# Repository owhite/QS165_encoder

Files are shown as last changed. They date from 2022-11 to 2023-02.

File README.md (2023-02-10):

# QS165 motor magentic encoder with hall output

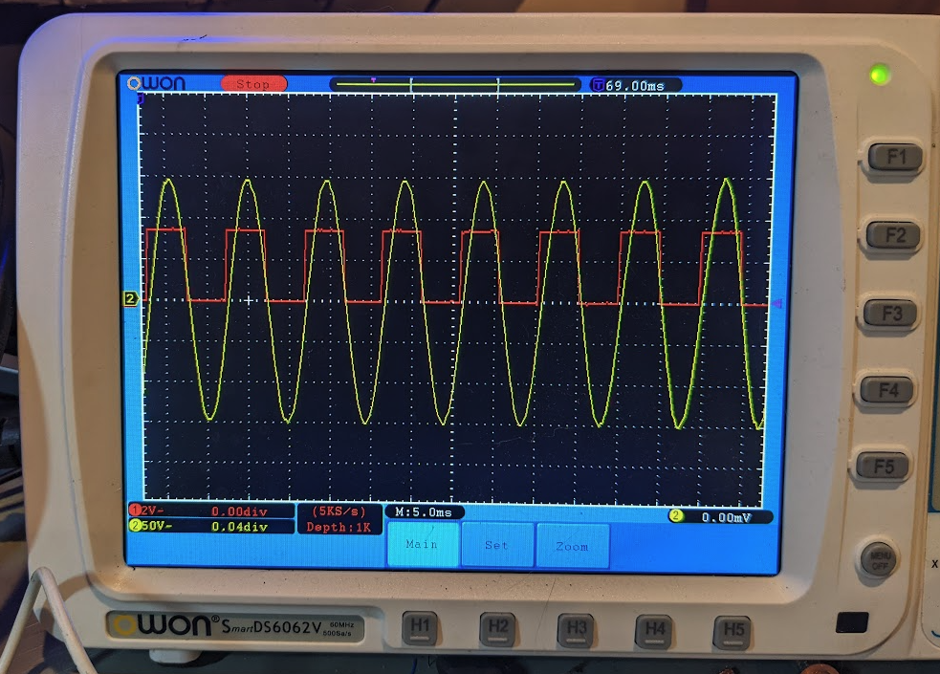
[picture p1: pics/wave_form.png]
phase plus encorder out

One scope probe (red) connected to "W" output of board, and another probe (yellow) is tied to the phase output of the QS165. The QS165 is turned by hand as described here: 

[LINK](https://github.com/badgineer/MP2-ESC/blob/main/docs/MOTOR_PARAM.md).

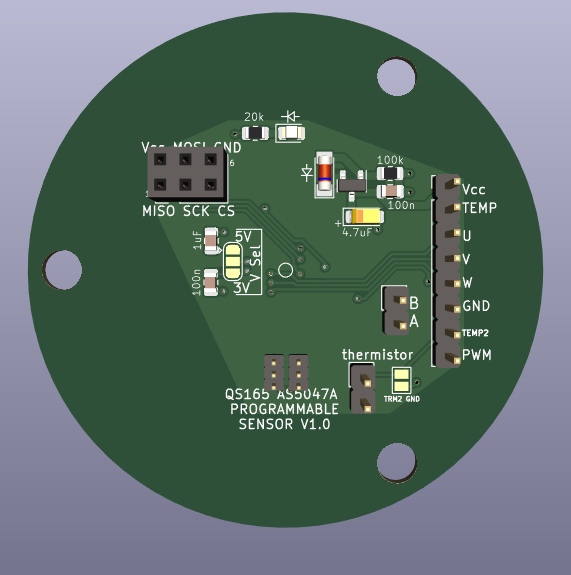
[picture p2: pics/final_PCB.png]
Encoder PCB


## An encoder retrofit for the QS165 motor [[See this link](AS5048_extburn/README.md)].

This encoder is designed as a drop in replacement to the QS165 motor and uses an AS5047 to generates UVW output. In order for this to work you'll need to program the AS5047 with an external CPU. So basically this is **unnecessarily expensive requiring purchase of a custum PCB and a teensy to program the board. It is unnecessarily complicated in that it requires a custom programmer dongle, common bench testing equipment, assembling a board, and knowledge of programming**. 

On the other hand I'm not aware of a lot of alternatives. 

### **Acknowledgement:**
* [CircularBuffer](https://github.com/CircularBuffer/AS5047P) supplied code to burn the AS5047 non-volatile memory.
* [David Molony](https://github.com/davidmolony) kindly helped with some development of early boards. 

## Schematic
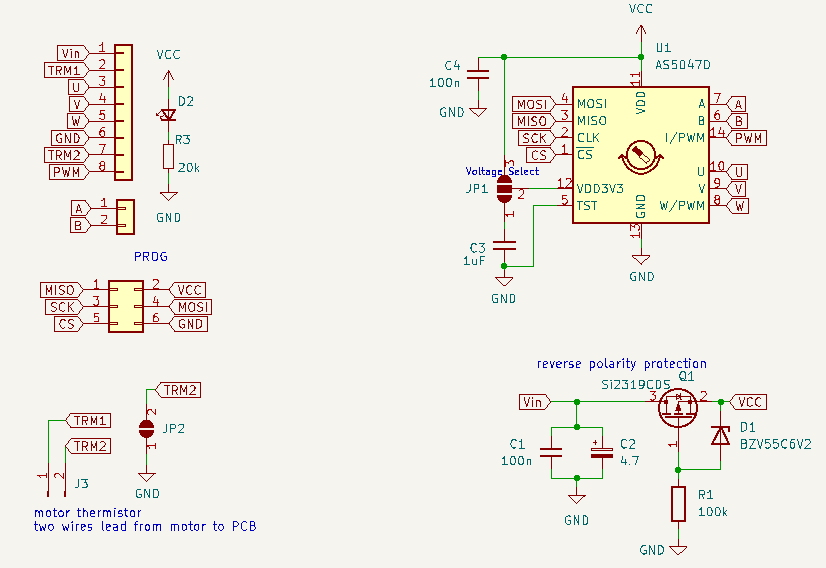
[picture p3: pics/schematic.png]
Schematic


## To build board and test
* Order and construct [this kicad board](AS5047_extburn/README.md)
* Create the programming dongle shown below
* Select between 3.3V versus 5V operation with solder jumper
* Please note: using 5V on the 3.3V definitely kills the chip
* Connect up up the finished PCB on the bench or motor
* Confirm the initial outputs of the AS5047 with an oscilloscope

## Programming
The AS5047 uses one time progromming to change some of it's registers permanantly. Note that programming definitely means you get **one time** to program the chip -- so be careful. 

As [CircularBuffer](https://github.com/CircularBuffer/AS5047P) points out, that code will probably work on a number of platforms. This works for me:

* Review [main.ino](https://github.com/owhite/QS165_encoder/tree/main/FIRMWARE/encoder/src/main.ino) carefully to understand how variables are sent to the AS5047 and the program flow
* Default variables for QS165 are set in main.ino using the lines:

```
  AS5047P_SetFieldInRegister(&encInstanceA, AS5047P_SETTINGS1, AS5047P_SETTINGS1_PWMON, 1);
  AS5047P_SetFieldInRegister(&encInstanceA, AS5047P_SETTINGS1, AS5047P_SETTINGS1_UVW_ABI, 1);
  AS5047P_SetFieldInRegister(&encInstanceA, AS5047P_SETTINGS2, AS5047P_SETTINGS2_UVWPP, 6);
```

Note: the QS165 has 7 polepairs, and according to the AS5047 docs you pass it a '6'. 

* Salt to taste if you have something else
* Load code on teensy board using the platformio environment to install [code](https://github.com/owhite/QS165_encoder/tree/main/FIRMWARE/encoder)
* Once programmed, connect teensy to encoder board using programming-dongle
* Start up a serial terminal
* While program is running, review the program is effectively communicating with the encoder board
* Confirm you like the actual output of the pins on encoder board
* Entering single characters into the serial input gets ready for the burn
* Typing anything besides "x" shows you serial input is working
* Enter "x" when youre ready to burn
* main.ino will report "no errors received, test if burn complete" if it worked
* Once it is programmed, youre done, and the AS5047 will not let you burn again.

## Programming hardware
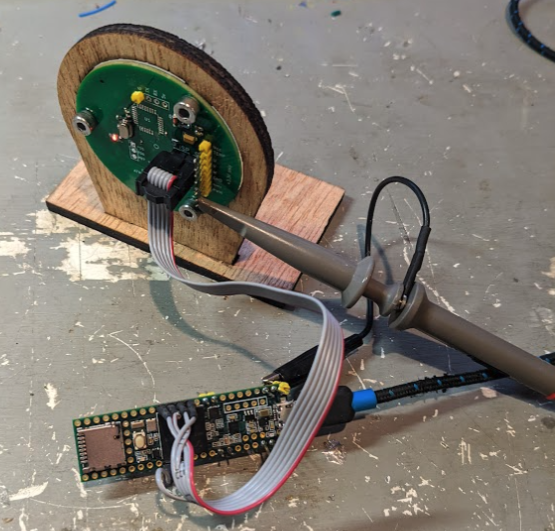
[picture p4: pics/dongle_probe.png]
Encoder programmer with scope probe


An example of programming a earlier version of the encoder board with a teensy 3.6, ribbon cable and 6 pin connector. 

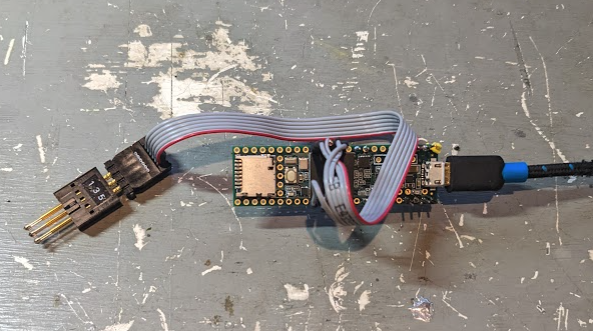
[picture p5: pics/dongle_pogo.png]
Encoder programmer with pogo pins


Pogo pins may be helpful for making quick connections to the board. 

## Shout out to my friends:
* Need a nice open source motor controller? Try the [MP2](https://github.com/badgineer/MP2-ESC). 
* Need some firmware to run on the motor controller? Try [MESC](https://github.com/davidmolony/MESC_Firmware). 
* A discussion of the QS165 on [endless-sphere](https://endless-sphere.com/forums/viewtopic.php?p=1748544).
* Two great sites for PCB and PCBA: [pcbway.com](https://www.pcbway.com/) and [jlcpcb.com](https://jlcpcb.com/).

## Final notes: some examples of other attempts to create an encoder
### **Attempt: AS5048 with line isolation [[LINK](AS5048_isolation/README.md)].**

Note: was not bad, just sort of complicated to use SPI with ESC.

### **Attempt: atmega328p to AS5048 [[LINK](AS5048_atmega328p/README.md)].**

Notes: Never really got this to work. 
* decoupling caps werent doing their job on original design which could be the cause;
* original xtal just didnt work;
* this may have resulted in serial writing bad characters;
* and programming problems. 

And, it's not clear the clock speed would ever be fast enough for SPI communications and reasonable output

PCB was set up for 5v. 

### **Attempt: AS5047 with on board CPU [[LINK](AS5047_atmega328p/README.md)].** 
This actually generated some reasonable output, but the downside it required the atmega to push SPI instructions to the AS5047.

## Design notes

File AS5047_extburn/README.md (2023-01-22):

# An encoder retrofit for the QS165 motor.

Review this [README](../README.md) for more information.

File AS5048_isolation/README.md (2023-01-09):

# QS165_encoder
QS165 encoder based on the TLE5012B encoder and galvanic isolators. 
No code is used for this project
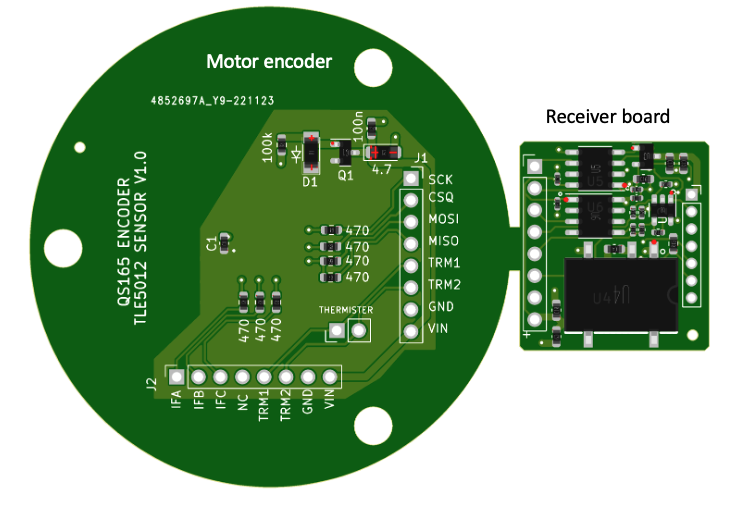
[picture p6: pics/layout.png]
sources of line noise

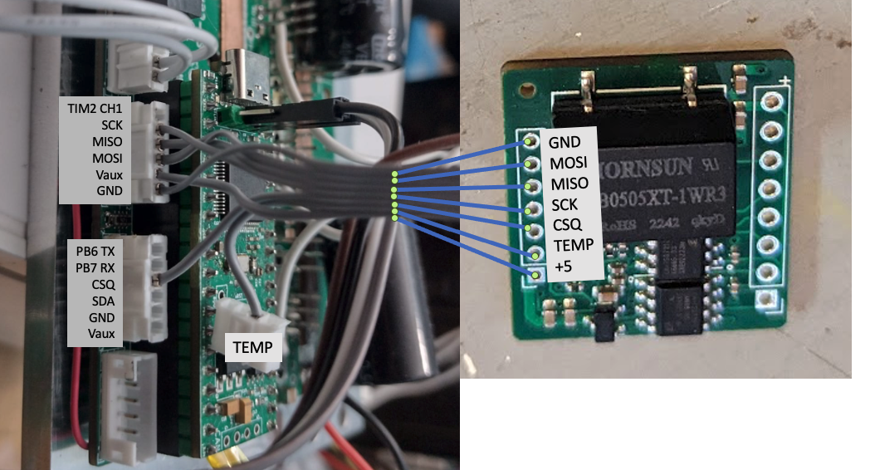
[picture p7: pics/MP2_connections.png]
MP2 connections


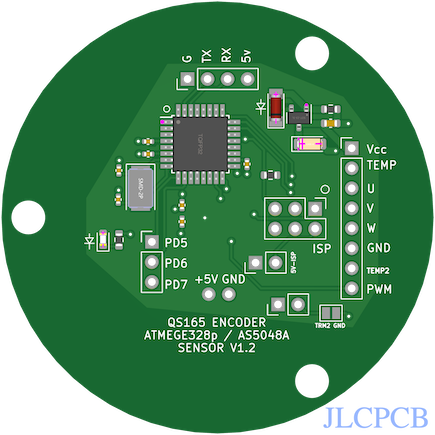
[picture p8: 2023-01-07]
pics/PCB_pic.png

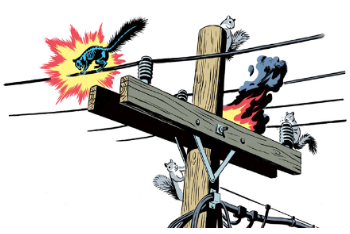
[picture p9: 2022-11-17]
pics/line_noise.png

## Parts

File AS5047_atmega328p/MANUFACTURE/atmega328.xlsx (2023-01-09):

Comment | Designator | Footprint | LCSC
100n | C1 | Capacitor_SMD:C_0603_1608Metric | C346191
4.7 | C2 | Capacitor_Tantalum_SMD:CP_EIA-3216-18_Kemet-A | C110055
100n | C3,C4,C5,C8 | Capacitor_SMD:C_0402_1005Metric | C1525
20p | C6,C7 | Capacitor_SMD:C_0402_1005Metric | C76959
BZV55C6V2 | D1 | Diode_SMD:D_MiniMELF | C266263
RED_LED | D2 | LED_SMD:LED_0603_1608Metric | C90692
Si2319CDS | Q1 | Package_TO_SOT_SMD:SOT-23 | C558254
100k | R1 | Resistor_SMD:R_0603_1608Metric | C14675
10k | R2 | Resistor_SMD:R_0603_1608Metric | C98220
20k | R3 | Resistor_SMD:R_0603_1608Metric | C365403
ATmega328P-AU | U1 | Package_QFP:TQFP-32_7x7mm_P0.8mm | C14877

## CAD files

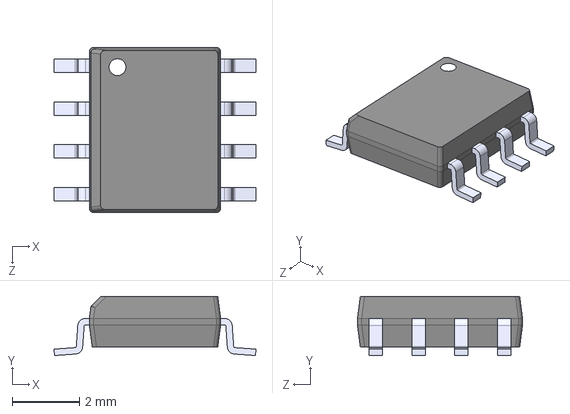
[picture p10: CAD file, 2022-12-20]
AS5047_extburn/LM386MX-1_NOPB/LM386MX-1_NOPB.step
5.99 x 1.75 x 4.90 mm

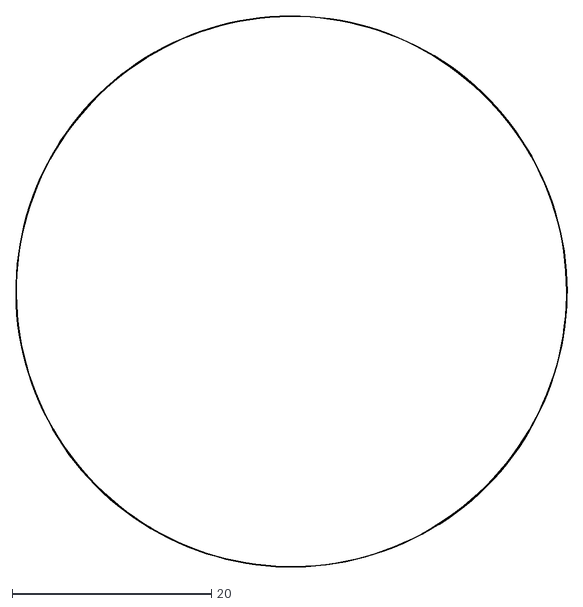
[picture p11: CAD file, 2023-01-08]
AS5048_atmega328p/DXFs/atmega328-Edge_Cuts.dxf
55.3 x 55.3

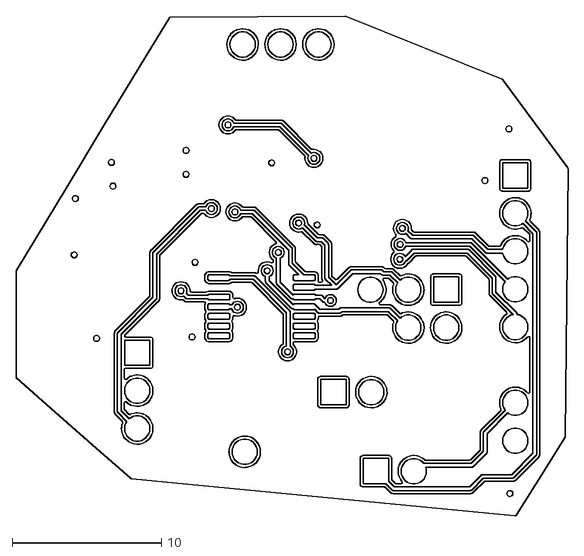
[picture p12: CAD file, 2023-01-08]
AS5048_atmega328p/DXFs/atmega328-B_Cu.dxf
37.0 x 33.5

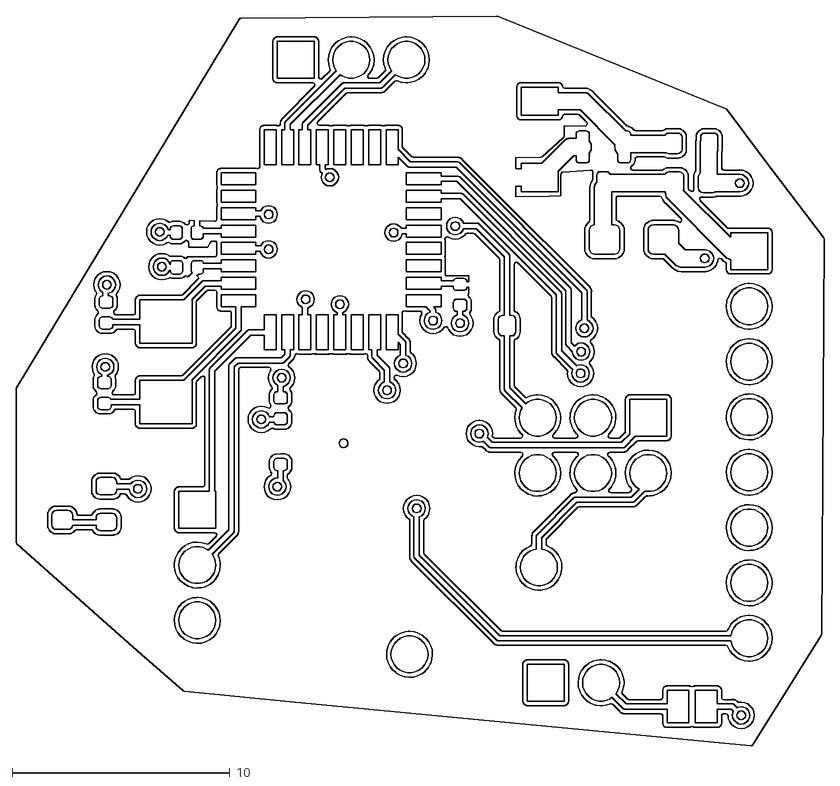
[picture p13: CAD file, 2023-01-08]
AS5048_atmega328p/DXFs/atmega328-F_Cu.dxf
37.1 x 33.5

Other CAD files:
AS5048_atmega328p/DXFs/atmega328-B_Mask.dxf
AS5048_atmega328p/DXFs/atmega328-B_Paste.dxf
AS5048_atmega328p/DXFs/atmega328-B_Silkscreen.dxf
AS5048_atmega328p/DXFs/atmega328-F_Mask.dxf
AS5048_atmega328p/DXFs/atmega328-F_Paste.dxf
AS5048_atmega328p/DXFs/atmega328-F_Silkscreen.dxf

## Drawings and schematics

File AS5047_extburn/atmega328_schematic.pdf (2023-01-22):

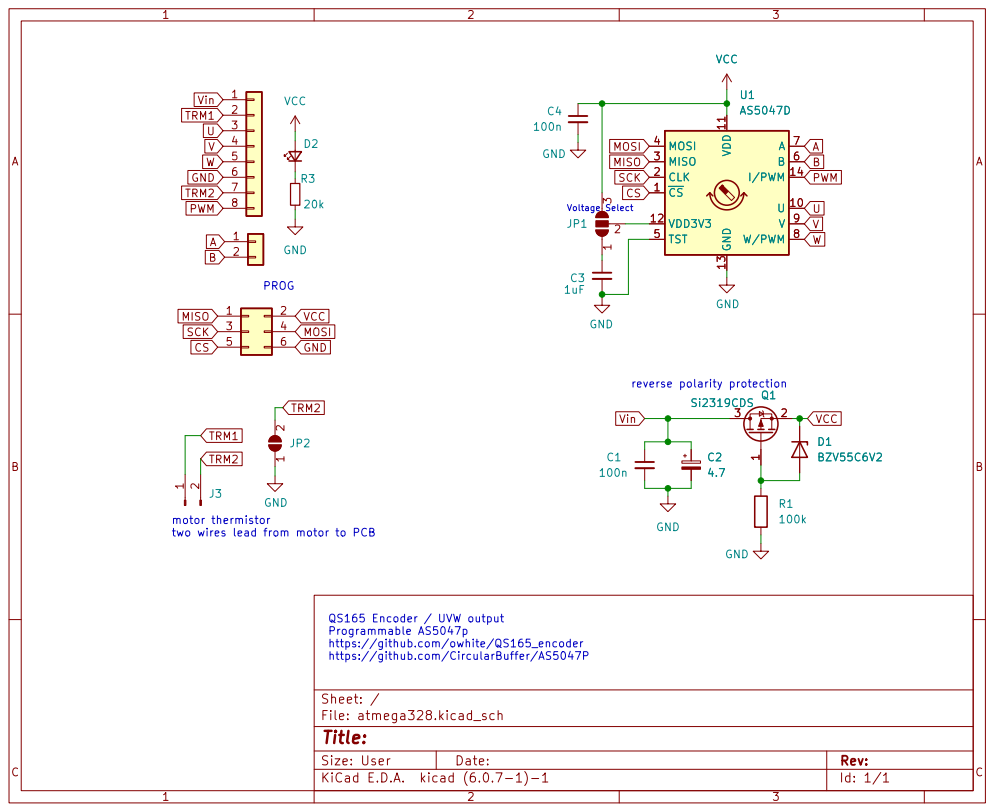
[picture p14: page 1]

MISO MOSI Voltage Select QS165 Encoder / UVW output

reverse polarity protection PROG

https://github.com/CircularBuffer/AS5047P motor thermistor
two wires lead from motor to PCB

Programmable AS5047p
https://github.com/owhite/QS165_encoder

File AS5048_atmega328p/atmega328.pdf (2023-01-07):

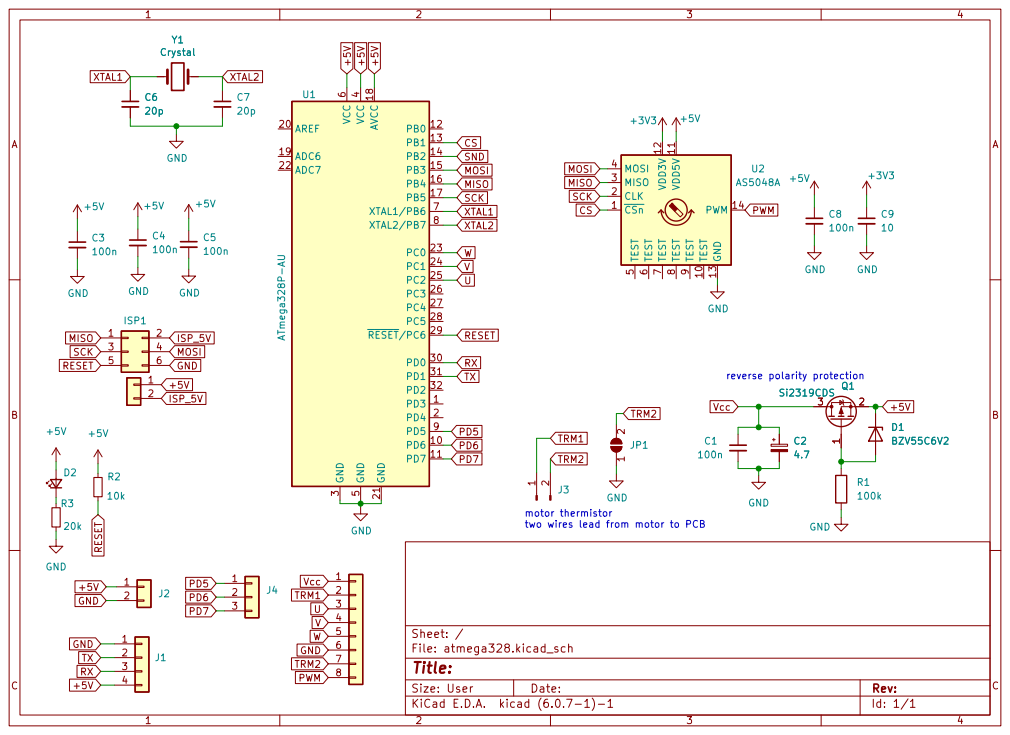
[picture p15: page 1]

two wires lead from motor to PCB

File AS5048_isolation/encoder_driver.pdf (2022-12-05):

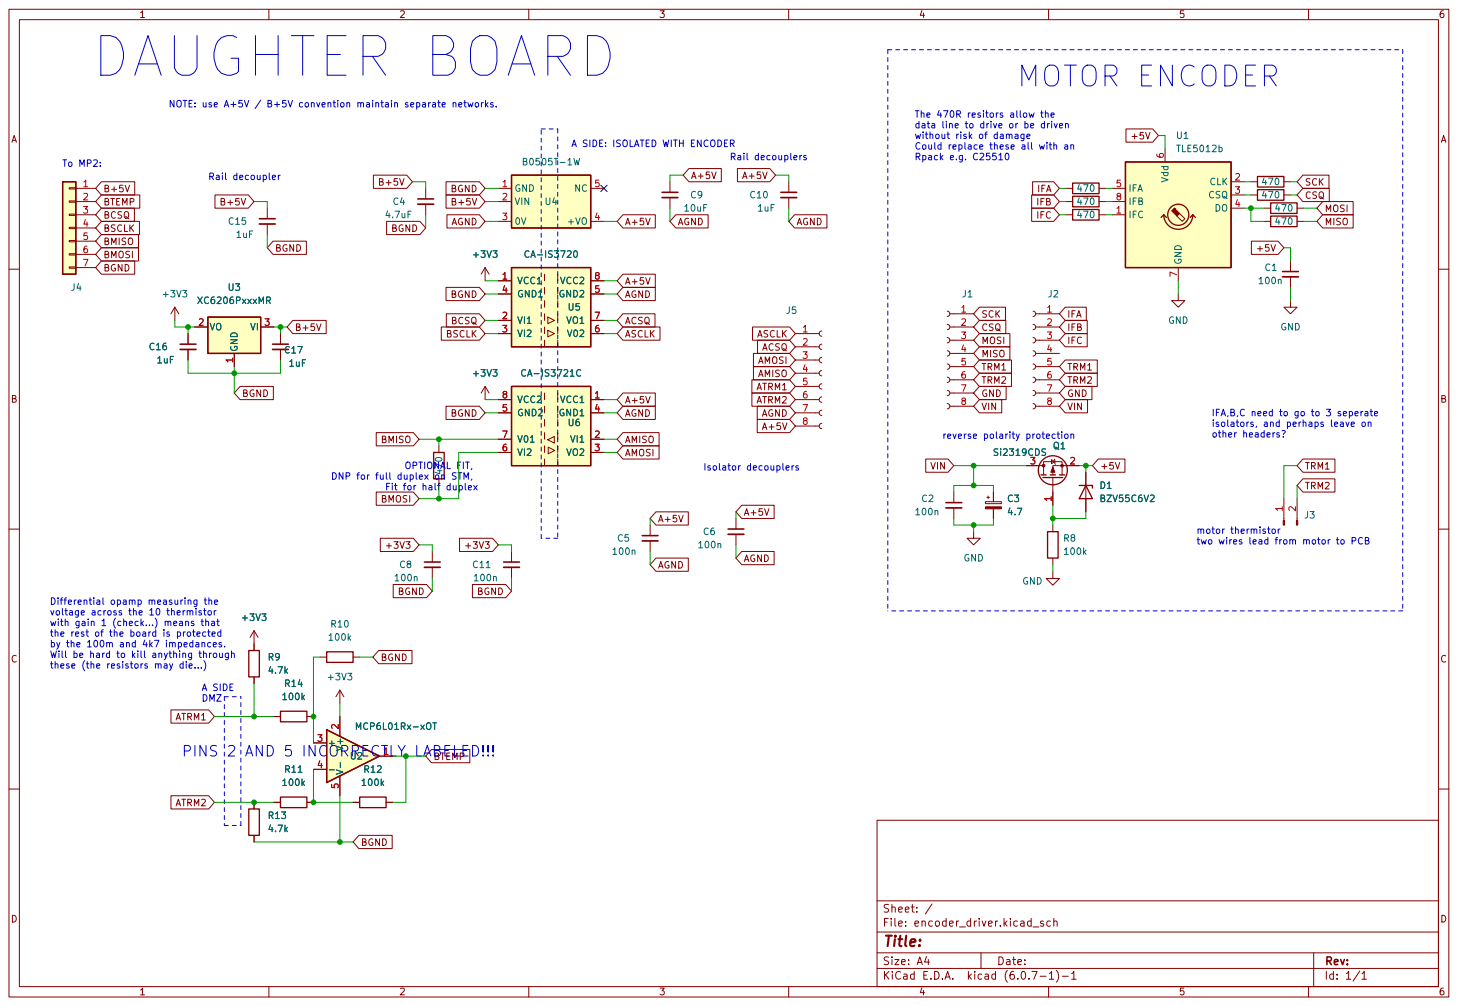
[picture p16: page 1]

isolators, and perhaps leave on other headers? The 470R resitors allow the data line to drive or be driven without risk of damage

Isolator decouplers A SIDE: ISOLATED WITH ENCODER

Could replace these all with an
Rpack e.g. C25510

IFA,B,C need to go to 3 seperate

PINS 2 AND 5 INCORRECTLY LABELED!!! OPTIONAL FIT, DNP for full duplex on STM,

two wires lead from motor to PCB

A SIDE DMZ Differential opamp measuring the
voltage across the 10 thermistor
with gain 1 (check...) means that
the rest of the board is protected
by the 100m and 4k7 impedances.
Will be hard to kill anything through
these (the resistors may die...)

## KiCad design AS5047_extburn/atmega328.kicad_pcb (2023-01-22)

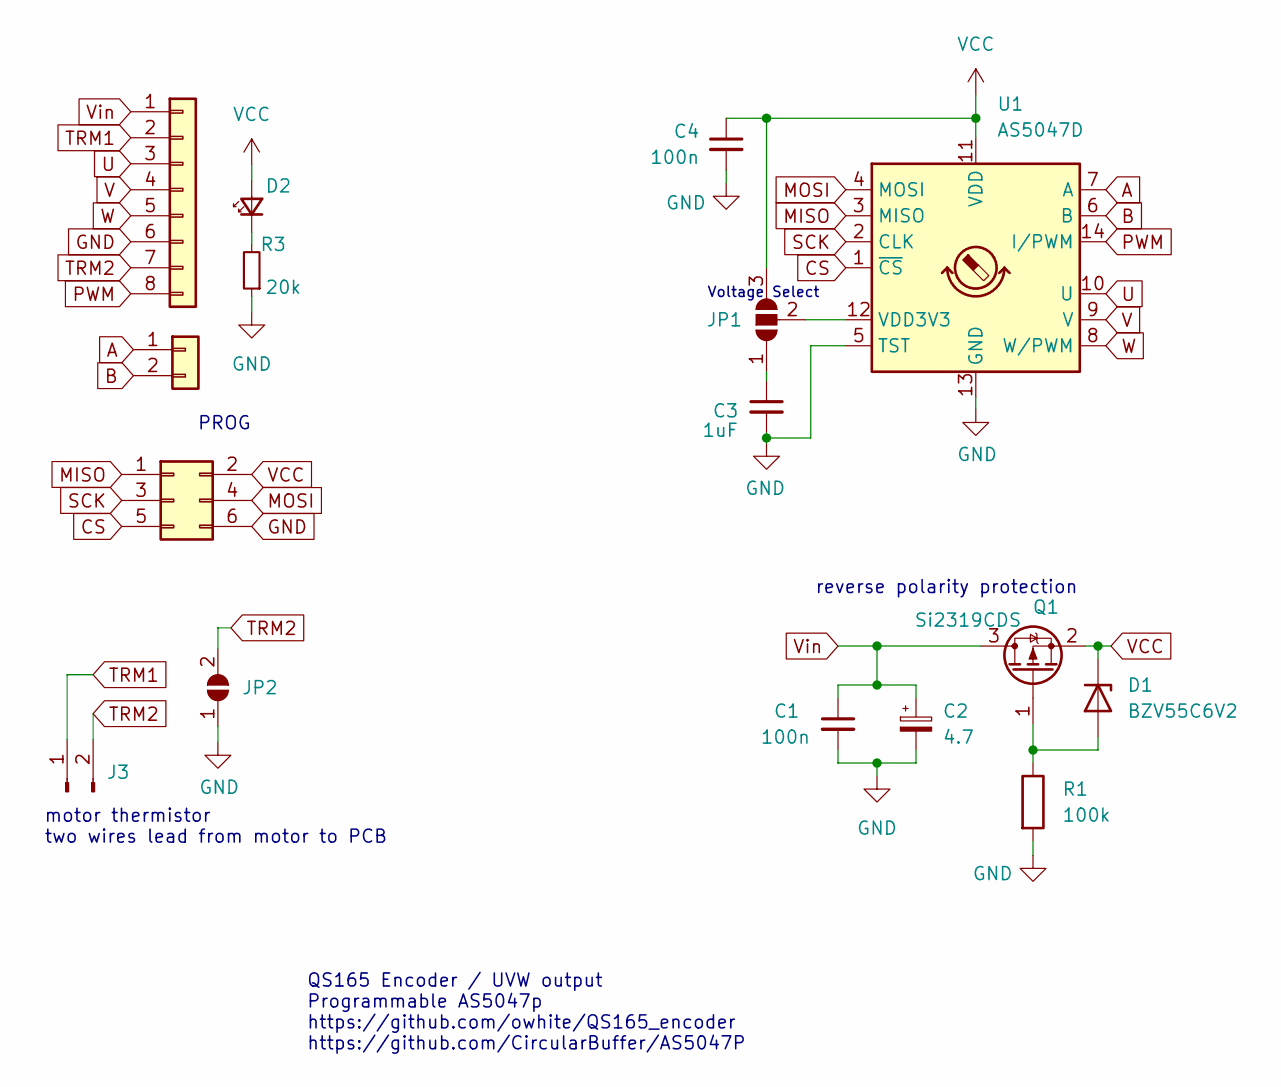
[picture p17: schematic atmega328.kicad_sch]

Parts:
C1, C4: 100n; C_0805_2012Metric
C2: 4.7; CP_EIA-3216-18_Kemet-A; LCSC C110055
C3: 1uF; C_0805_2012Metric
D1: BZV55C6V2; D_MiniMELF; LCSC C266263
D2: RED_LED; LED_0805_2012Metric
J1: Conn_01x02; PinHeader_1x02_P2.54mm_Vertical
J3: Conn_01x02_Male; PinHeader_1x02_P2.54mm_Vertical
J5: Conn_01x08; PinHeader_1x08_P2.54mm_Vertical
JP1: SolderJumper_3_Open; SolderJumper-3_P1.3mm_Open_RoundedPad1.0x1.5mm
JP2: SolderJumper_2_Open; SolderJumper-2_P1.3mm_Open_Pad1.0x1.5mm
PRG1: Conn_02x03_Top_Bottom; isp_6pin
Q1: Si2319CDS; SOT-23; LCSC C558254
R1: 100k; R_0805_2012Metric
R3: 20k; R_0805_2012Metric
U1: AS5047D; TSSOP-14_4.4x5mm_P0.65mm

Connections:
A: J1.1, U1.7 (A)
B: J1.2, U1.6 (B)
CS: PRG1.5, U1.1 (~CS)
GND: C1.2, C2.2, C3.2, C4.2, J5.6, JP2.1 (A), PRG1.6, R1.2, R3.1, U1.5 (TST), U1.13 (GND)
MISO: PRG1.1, U1.3 (MISO)
MOSI: PRG1.4, U1.4 (MOSI)
unnamed: C3.1, JP1.1 (A)
unnamed: D1.2 (A), Q1.1 (G), R1.1
unnamed: D2.1 (K), R3.2
unnamed: JP1.2 (C), U1.12 (VDD3V3)
PWM: J5.8, U1.14 (I/PWM)
SCK: PRG1.3, U1.2 (CLK)
TRM1: J3.1, J5.2
TRM2: J3.2, J5.7, JP2.2 (B)
U: J5.3, U1.10 (U)
V: J5.4, U1.9 (V)
VCC: C4.1, D1.1 (K), D2.2 (A), JP1.3 (B), PRG1.2, Q1.2 (S), U1.11 (VDD)
Vin: C1.1, C2.1, J5.1, Q1.3 (D)
W: J5.5, U1.8 (W/PWM)

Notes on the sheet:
QS165 Encoder / UVW output Programmable AS5047p https://github.com/owhite/QS165_encoder https://github.com/CircularBuffer/AS5047P
motor thermistor two wires lead from motor to PCB
PROG
reverse polarity protection
Voltage Select

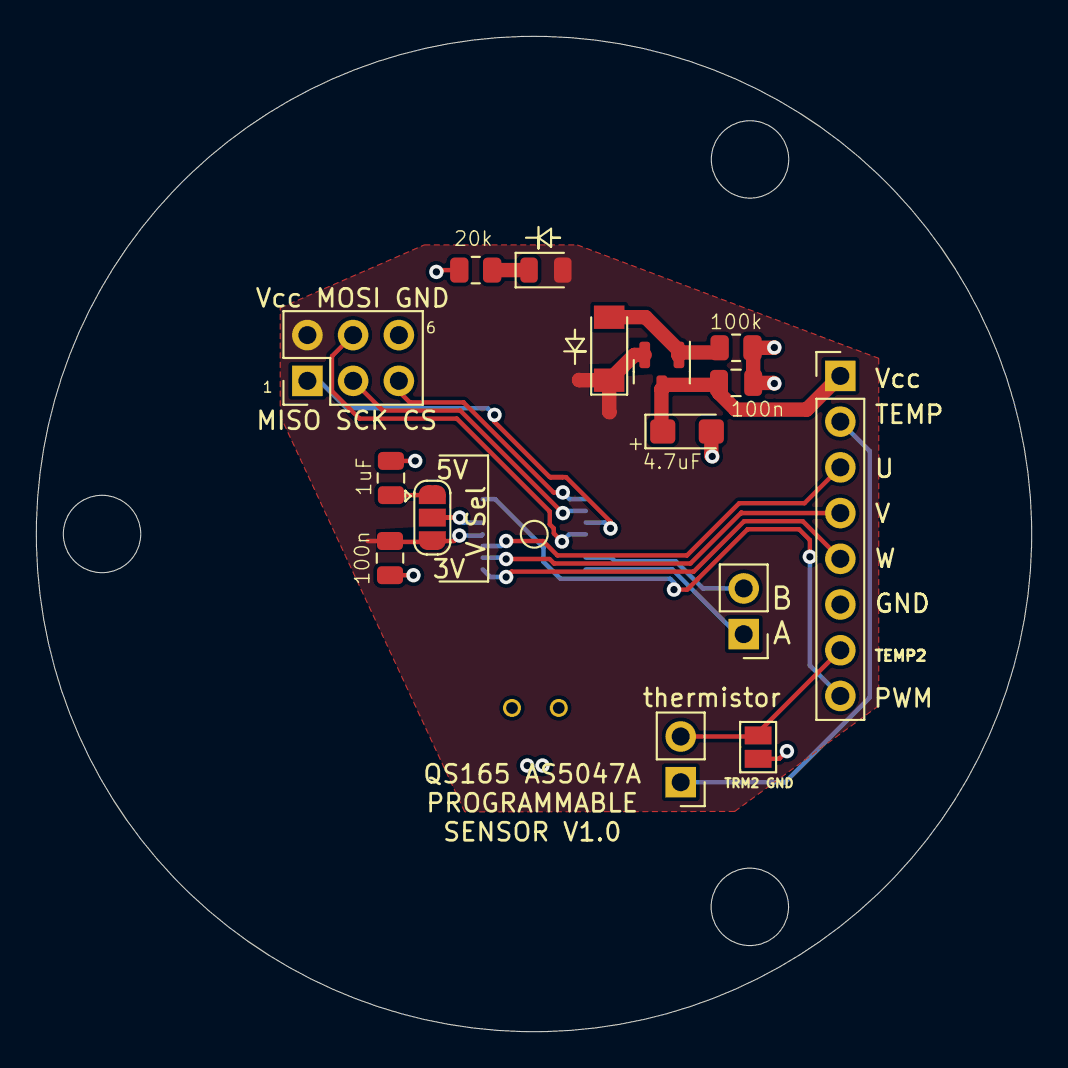
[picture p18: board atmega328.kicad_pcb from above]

Board: 2 copper layers, 55.3 x 55.3 mm, 16 parts (1 on the bottom side), 19 nets.

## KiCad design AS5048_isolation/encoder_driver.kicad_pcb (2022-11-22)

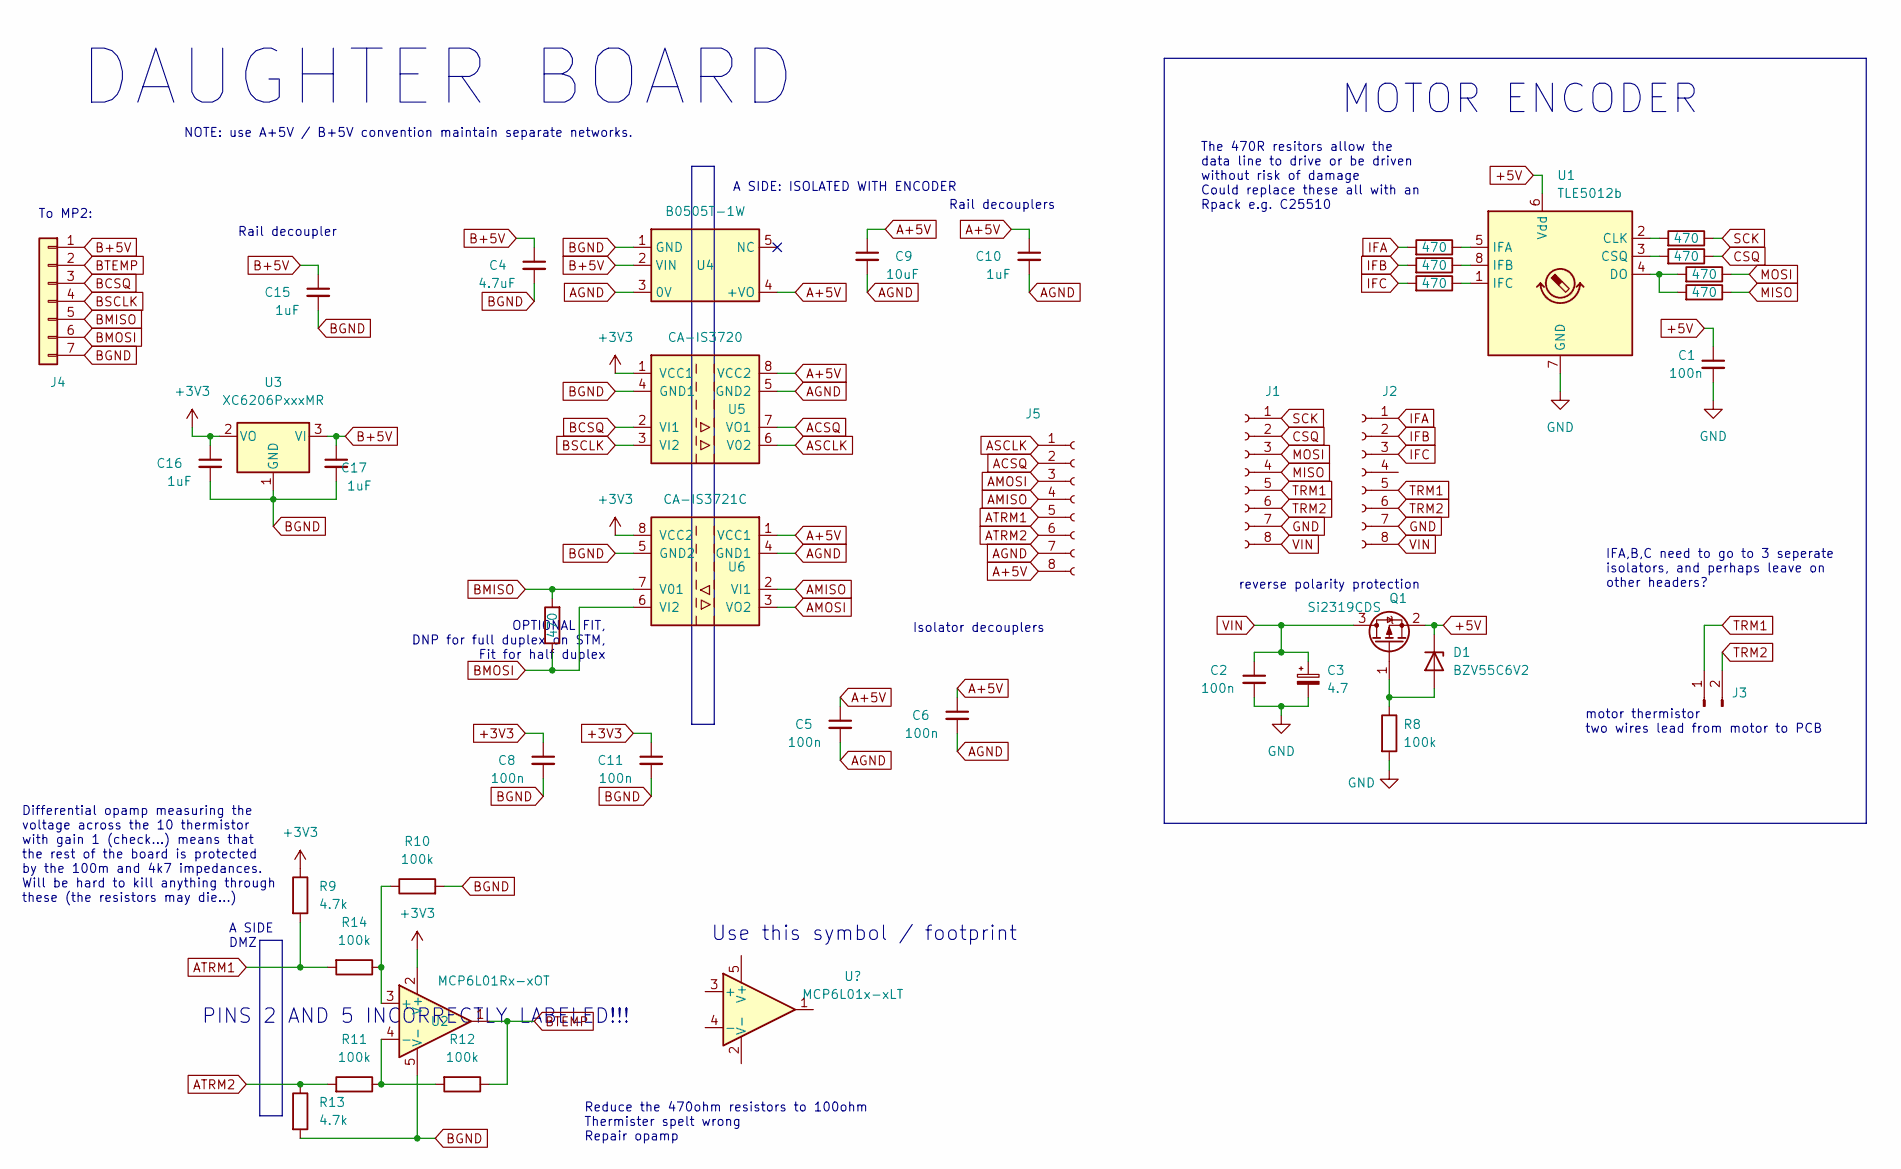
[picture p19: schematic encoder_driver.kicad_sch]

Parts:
C1, C2: 100n; C_0603_1608Metric; LCSC C346191
C3: 4.7; CP_EIA-3216-18_Kemet-A; LCSC C110055
C4: 4.7uF; C_0603_1608Metric; LCSC C15849
C5, C6, C8, C11: 100n; C_0402_1005Metric; LCSC C361203
C9: 10uF; C_0603_1608Metric; LCSC C15849
C10, C15, C16, C17: 1uF; C_0603_1608Metric; LCSC C15849
D1: BZV55C6V2; D_MiniMELF; LCSC C266263
J1, J2: Conn_01x08_Female; PinSocket_1x08_P2.54mm_Vertical
J3: Conn_01x02_Male; PinHeader_1x02_P2.54mm_Vertical
J4: Conn_01x07; PinSocket_1x07_P2.00mm_Vertical
J5: Conn_01x08_Female; PinHeader_1x08_P2.54mm_Vertical
Q1: Si2319CDS; SOT-23; LCSC C558254
R1, R2, R3, R4, R5, R6, R7, R15: 470; R_0603_1608Metric; LCSC C23179
R8: 100k; R_0603_1608Metric; LCSC C14675
R9, R13: 4.7k; R_0402_1005Metric; LCSC C103055
R10, R11, R12, R14: 100k; R_0402_1005Metric; LCSC C269673
U1: TLE5012b; my_Infineon_PG-DSO-8
U2: MCP6L01Rx-xOT; SOT-23-5; LCSC C693056
U3: XC6206PxxxMR; SOT-23; LCSC C5446
U4: B0505T-1W; PWRM-SMD_B0505XT-1WR2; LCSC C30338
U5: CA-IS3720; SOIC-8_3.9x4.9mm_P1.27mm; LCSC C428882
U6: CA-IS3721C; SOIC-8_3.9x4.9mm_P1.27mm; LCSC C5121216

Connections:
+3V3: C8.1, C11.1, C16.1, R9.1, U2.2 (V+), U3.2 (VO), U5.1 (VCC1), U6.8 (VCC2)
+5V: C1.1, D1.1 (K), Q1.2 (S), U1.6 (Vdd)
A+5V: C5.1, C6.1, C9.1, C10.1, J5.8, U4.4 (+VO), U5.8 (VCC2), U6.1 (VCC1)
ACSQ: J5.2, U5.7 (VO1)
AGND: C5.2, C6.2, C9.2, C10.2, J5.7, U4.3 (0V), U5.5 (GND2), U6.4 (GND1)
AMISO: J5.4, U6.2 (VI1)
AMOSI: J5.3, U6.3 (VO2)
ASCLK: J5.1, U5.6 (V02)
ATRM1: J5.5, R9.2, R14.2
ATRM2: J5.6, R11.2, R13.1
B+5V: C4.1, C15.1, C17.1, J4.1, U3.3 (VI), U4.2 (VIN)
BCSQ: J4.3, U5.2 (VI1)
BGND: C4.2, C8.2, C11.2, C15.2, C16.2, C17.2, J4.7, R10.2, R13.2, U2.5 (V-), U3.1 (GND), U4.1 (GND), U5.4 (GND1), U6.5 (GND2)
BMISO: J4.5, R15.2, U6.7 (V01)
BMOSI: J4.6, R15.1, U6.6 (VI2)
BSCLK: J4.4, U5.3 (VI2)
BTEMP: J4.2, R12.1, U2.1
CSQ: J1.2, R5.1
GND: C1.2, C2.2, C3.2, J1.7, J2.7, R8.2, U1.7 (GND)
IFA: J2.1, R1.2
IFB: J2.2, R2.2
IFC: J2.3, R3.2
MISO: J1.4, R7.1
MOSI: J1.3, R6.1
unnamed: D1.2 (A), Q1.1 (G), R8.1
unnamed: R1.1, U1.5 (IFA)
unnamed: R2.1, U1.8 (IFB)
unnamed: R3.1, U1.1 (IFC)
unnamed: R4.2, U1.2 (CLK)
unnamed: R5.2, U1.3 (CSQ)
unnamed: R6.2, R7.2, U1.4 (DO)
unnamed: R10.1, R14.1, U2.3 (+)
unnamed: R11.1, R12.2, U2.4 (-)
SCK: J1.1, R4.1
TRM1: J1.5, J2.5, J3.1
TRM2: J1.6, J2.6, J3.2
VIN: C2.1, C3.1, J1.8, J2.8, Q1.3 (D)

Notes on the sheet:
MOTOR ENCODER
motor thermistor two wires lead from motor to PCB
Rail decoupler
Reduce the 470ohm resistors to 100ohm Thermister spelt wrong Repair opamp
PINS 2 AND 5 INCORRECTLY LABELED!!!
Differential opamp measuring the voltage across the 10 thermistor with gain 1 (check...) means that the rest of the board is protected by the 100m and 4k7 impedances. Will be hard to kill anything through these (the resistors may die...)
reverse polarity protection
To MP2:
A SIDE DMZ
Rail decouplers
OPTIONAL FIT, DNP for full duplex on STM, Fit for half duplex
DAUGHTER BOARD
IFA,B,C need to go to 3 seperate isolators, and perhaps leave on other headers?
NOTE: use A+5V / B+5V convention maintain separate networks.
Isolator decouplers
Use this symbol / footprint
A SIDE: ISOLATED WITH ENCODER
The 470R resitors allow the data line to drive or be driven without risk of damage Could replace these all with an Rpack e.g. C25510

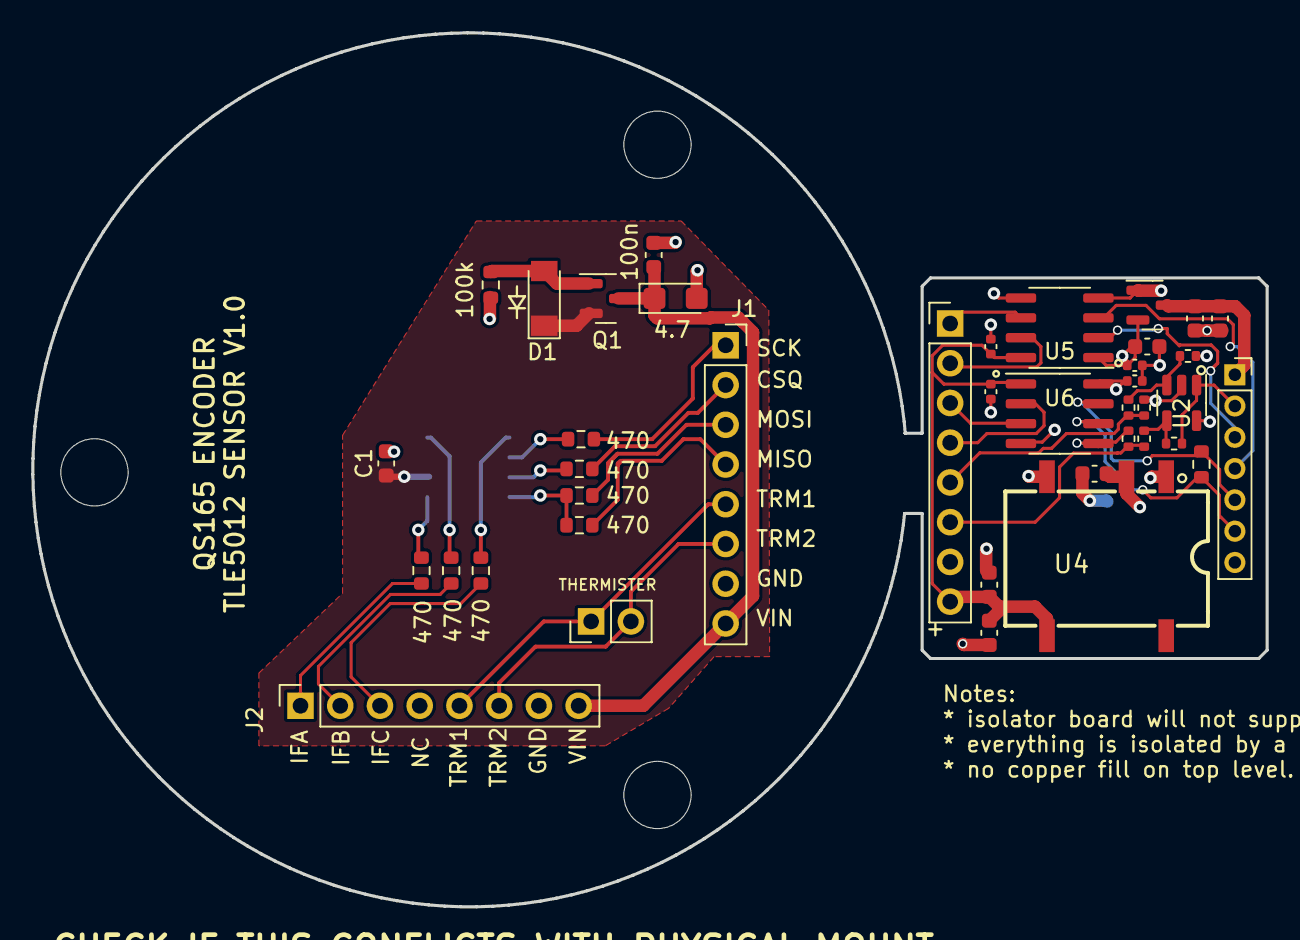
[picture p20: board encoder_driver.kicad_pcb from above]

Board: 4 copper layers, 78.9 x 55.9 mm, 41 parts (1 on the bottom side), 37 nets.

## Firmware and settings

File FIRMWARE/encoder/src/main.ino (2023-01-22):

#include "as5047p.h"
#include "SPI.h"

AS5047P_Instance encInstanceA;
AS5047P_Result encPositionA;

void setup() {
  pinMode(10, OUTPUT);  
  SPI.begin();
  
  AS5047P_Init(&encInstanceA, 1); // 1 requires cs = 10

  AS5047P_SetFactorySettings(&encInstanceA);

  AS5047P_SetZeroPosition(&encInstanceA);  

  AS5047P_SetFieldInRegister(&encInstanceA, AS5047P_SETTINGS1, AS5047P_SETTINGS1_PWMON, 1);

  AS5047P_SetFieldInRegister(&encInstanceA, AS5047P_SETTINGS1, AS5047P_SETTINGS1_UVW_ABI, 1);

  AS5047P_SetFieldInRegister(&encInstanceA, AS5047P_SETTINGS2, AS5047P_SETTINGS2_UVWPP, 6);
}

int isKthBitSet(int n, int k) {
    if (n & (1 << k))
      return 1;
    else
      return 0;
}

void loop2() {

}

void loop() {

  encPositionA = AS5047P_ReadPosition(&encInstanceA, AS5047P_OPT_ENABLED);

  if( !AS5047P_ErrorPending(&encInstanceA) )
  {
    //--- the block reports if chip is connected, and settings are right for burn
    Serial.print("Encoder ID[");
    Serial.print( AS5047P_GetID(&encInstanceA) );
    Serial.print("]> Position: ");
    Serial.println( (uint16_t)encPositionA );
    Serial.print("]> PWMON: ");
    Serial.println( isKthBitSet(AS5047P_ReadRegister(&encInstanceA, AS5047P_SETTINGS1, AS5047P_OPT_ENABLED), 7) );
    Serial.print("]> UVW_ABI: ");
    Serial.println( isKthBitSet(AS5047P_ReadRegister(&encInstanceA, AS5047P_SETTINGS1, AS5047P_OPT_ENABLED), 3) );

    int val = AS5047P_ReadRegister(&encInstanceA, AS5047P_SETTINGS2, AS5047P_OPT_ENABLED);
    val <<= 5;
    val >>= 5;
    Serial.print("]> PP: ");
    Serial.println( val );


  }
  else
  {
    //--- Some thing is wrong -- print error messages
    Serial.print("Encoder ID[");
    Serial.print( AS5047P_GetID(&encInstanceA) );
    Serial.print("]> Error ");
    Serial.print( AS5047P_GetError(&encInstanceA).errorCode );
    Serial.print(" : ");
    Serial.println(AS5047P_GetError(&encInstanceA).msg);

    AS5047P_ErrorAck(&encInstanceA);
  }

  // user can initiate burn by sending single characters over serial. 
  if (Serial.available() > 0) {
    int ByteReceived = Serial.read();
    
    // If user sends "x" over serial, initiate burn
    if (ByteReceived == 120) { 
      int result = AS5047P_BurnOTP(&encInstanceA, 666);
      Serial.println("]>BURN!");
      if (result == 0) {
	Serial.println(" no errors received, test if burn complete");
      }
      else {
	Serial.print(" something failed:"); Serial.println(result);
      }

      while(1){}
    }
    else if (ByteReceived == 13) {
      // end of line, ignore
    }
    else { // user sent something else
      Serial.print("type X to burn");
      delay(1000);
    }
  
  }

  delay(800);    
}

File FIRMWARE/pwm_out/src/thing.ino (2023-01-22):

#include <AS5048A.h>

#define PinB0 8
#define PinB1 9
#define PinB2 10
#define PinB3 11
#define PinB4 12
#define PinB5 13

#define PinC0 14
#define PinC1 15
#define PinC2 16
#define PinC3 17
#define PinC4 18
#define PinC5 19

#define PinD0 0
#define PinD1 1
#define PinD2 2
#define PinD3 3
#define PinD4 4
#define PinD5 5
#define PinD6 6
#define PinD7 7


// AS5048A angleSensor(PinB1, true);
AS5048A angleSensor(10, false);

int led_state = 0;
int count = 0;
void setup() {
  delay(100);

  pinMode(13,OUTPUT);

  angleSensor.begin();

  Serial.begin(9600);
}

void loop() {

  led_state =! led_state;

  float val = angleSensor.getRotationInDegrees();
  delay(100);
  Serial.println(val);

  int x = int(val);
  // analogWrite(PinD5, map(x, 0, 360, 0, 255));
  // analogWrite(PinD5, int(val));
}

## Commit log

2022-10-11 initiate project
    [encoder_driver.kicad_pcb, encoder_driver.kicad_sch]
2022-10-11 edit schematic
    [encoder_driver.kicad_sch]
2022-11-02 lots of layout
    [encoder_driver.kicad_pcb, encoder_driver.kicad_sch]
2022-11-02 added outline
    [encoder_driver.kicad_pcb]
2022-11-17 TLE5012 encoder initialization
    [encoder_driver.kicad_pcb]
2022-11-18 added isolators
    [encoder_driver.kicad_pcb, encoder_driver.kicad_sch]
2022-11-19 DMM Add opamp based thermistor measurement prototype Half duplex SPI option for encoder 3v3 for output to F405 board (does not like 5V on some inputs) Some component assignments to LCSC numbers
    [encoder_driver.kicad_sch]
2022-11-22 near final draft
    [Untitled.dxf, encoder_driver-B_Cu.dxf, encoder_driver-B_Mask.dxf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]
2022-11-22 submitted to jlcpcb
    [Untitled.dxf, encoder_driver-B_Cu.dxf, encoder_driver-B_Mask.dxf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]
2022-12-05 error with U2
    [encoder_driver.kicad_sch]
2022-12-20 created new version
    [encoder_driver-B_Cu.gbr, encoder_driver-B_Mask.gbr, encoder_driver-B_Paste.gbr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]
2022-12-20 created V1.1
    [LM386MX-1_NOPB.step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]
2023-01-06 recreating lost AS5048 version
    [atmega328-B_Cu.gbr, atmega328-B_Mask.gbr, atmega328-B_Paste.gbr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]
2023-01-07 JCLPCB V1.2 order
    [LM386MX-1_NOPB.step, atmega328-BOM.xlsx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]
2023-01-07 added firmware
    [atmega328.csv]
2023-01-08 new notes
    [atmega328-B_Cu.dxf, atmega328-B_Mask.dxf, atmega328-B_Paste.dxf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]
2023-01-22 new documentation
    [LM386MX-1_NOPB.step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]
